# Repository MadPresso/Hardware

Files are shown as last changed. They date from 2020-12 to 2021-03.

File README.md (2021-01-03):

# MadPresso

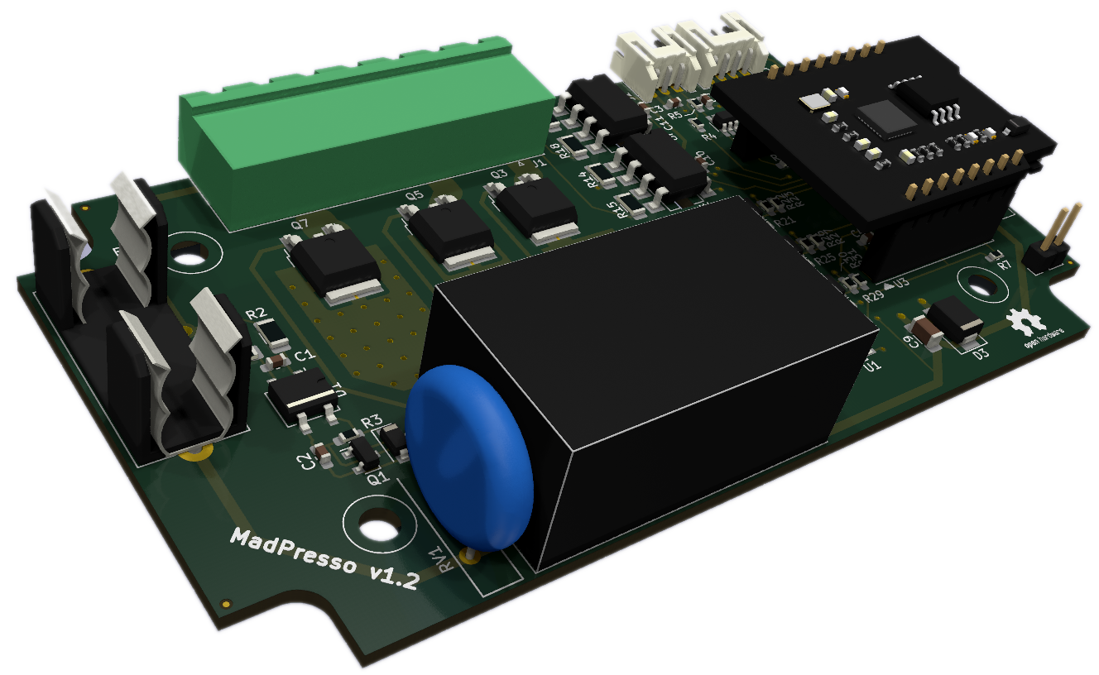
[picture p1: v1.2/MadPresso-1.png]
3D image of PCB


MadPresso is an open-hardware [PID controller](https://en.wikipedia.org/wiki/PID_controller) for espresso machines, based on an ESP8266 module. It was developed for a [Rancilio Silvia](https://www.ranciliogroup.com/rancilio/silvia/silvia/) machine but is likely usable with other brands as well.

This repository contains the [KiCad](https://kicad.org) hardware design files

Open Hardware logo
KiCad logo

# Features

* Compatible with 110 VAC and 230 VAC mains, both 50 Hz and 60 Hz
* ESP8266 module for controlling logic, Wifi and logging
* Fused 5V power supply
* Zero-crossing logic for phase-cutting time base
* 2 Triac outputs for LINE switching
* 1 Triac output for NEUTRAL switching
* 2 main voltage monitors on LINE
* 3-pin JST connector for LM35DT temperature sensor
* 4-pin JST connector for general purpose peripherals such as an OLED display

# Functionality

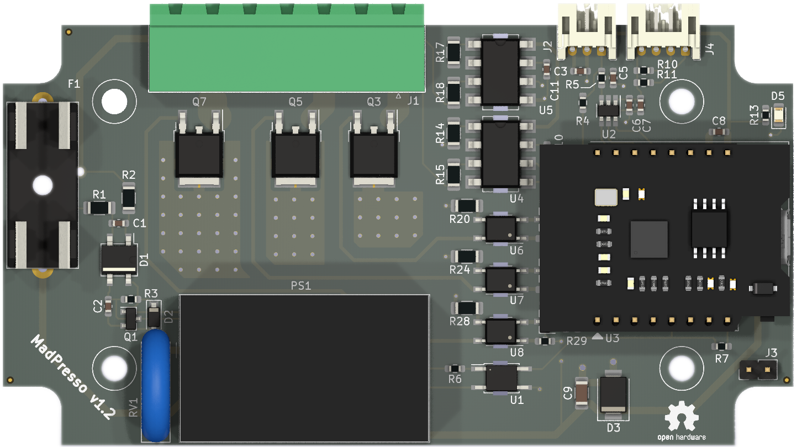
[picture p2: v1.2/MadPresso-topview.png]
PCB top view


The design features a zero-crossing detection circuitry that generates short spikes of low pulses around the point in time when the mains voltages crosses the zero-point. This signal is fed to the ESP8266 module which uses it to reset the triac ignition timer. Refer to the [firmware project](https://github.com/MadPresso/Firmware) for more details.

The boiler temperature is measured with an [LM35DT](https://www.ti.com/lit/ds/symlink/lm35.pdf) and sampled with a 10-bit ADC. The value is used as input to the PID logic implemented in the [firmware](https://github.com/MadPresso/Firmware).

Triac are controlled by the firmware as well, and isolated from the digital part through optocouplers.

Two line-monitor voltage sensors are used to detect the state of the "Shot" and "Steam" switches. Both are isolated from the digital logic through optocouplers as well.

# Pinout

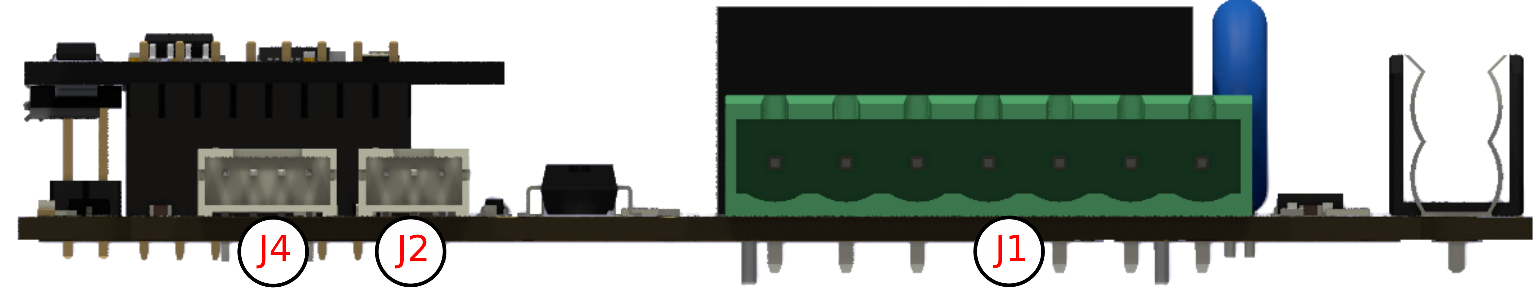
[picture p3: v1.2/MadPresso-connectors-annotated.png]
Connectors view annotated


The connectors located on the upper side of the PCB have the following functions. Note that pin 1 is on the left side of the connector when looked at as shown in the picture.

## J1

This connector carries all the 230 VAC mains functions. 
The mating part is an [RS Pro 8971222 Pluggable Rising Clamp Terminal](https://docs.rs-online.com/e4b6/0900766b8157d651.pdf).

1. Triac switch contact for NEUTRAL switching (LINE is permantely connected at the consumer). This pin is used to switch the **pump** on the Rancilio Silvia model.
2. NEUTRAL mains connection
3. Triac switch contact for LINE switchon (NEUTRAL is permanently connected at the consumer). This pin is used to switch the **valve** on the Rancilio Silvia model.
4. Shot switch LINE end
5. Steam switch LINE end
6. Triac switch contact for LINE switchon (NEUTRAL is permanently connected at the consumer). This pin is used to switch the **heater** on the Rancilio Silvia model.
7. LINE mains connection

## J2

This connector is intended to be used with an [LM35DT](https://www.ti.com/lit/ds/symlink/lm35.pdf) analog temperature sensor.
The mating part is a 3-pin, 2mm pitch [JST PH](http://www.jst-mfg.com/product/detail_e.php?series=199) plug.

1. Analog temperature input pin
2. GND
3. +5V

## J4

This connector is a general-purpose I²C extension that may be used to connect an OLED display, for instance.
The mating part is a 4-pin, 2mm pitch [JST PH](http://www.jst-mfg.com/product/detail_e.php?series=199) plug.

1. SDA
2. SCL
3. GND
4. +3.3V

# Housing

The PCB is made to fit into a [Hammond 1591XXBT](http://hammondmfg.com/dwg2XX.htm) plastic case. Cut-outs need to be milled into the case for the connectors.

# Schematics

The schematics are provided as [PDF](https://github.com/MadPresso/Hardware/blob/main/v1.2/MadPresso.pdf) and as KiCad design file.

# License

The design is released under the [CC-BY-SA-NC license](https://creativecommons.org/licenses/by-nc-sa/3.0/). Commercial use is hence prohibited.

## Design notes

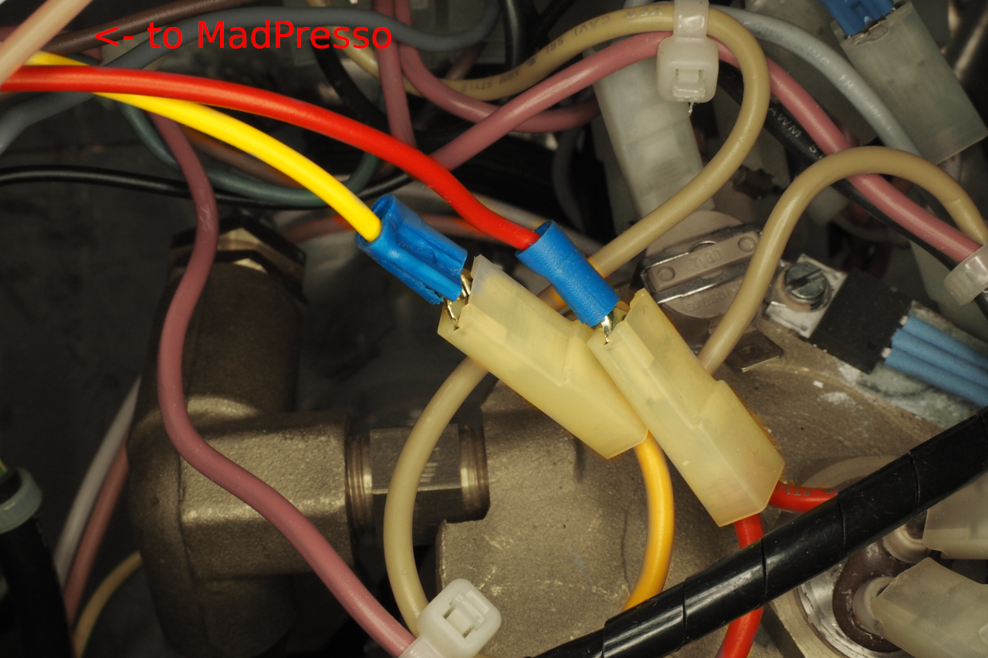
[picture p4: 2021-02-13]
doc/RancilioSilvia/connection-red-yellow.png

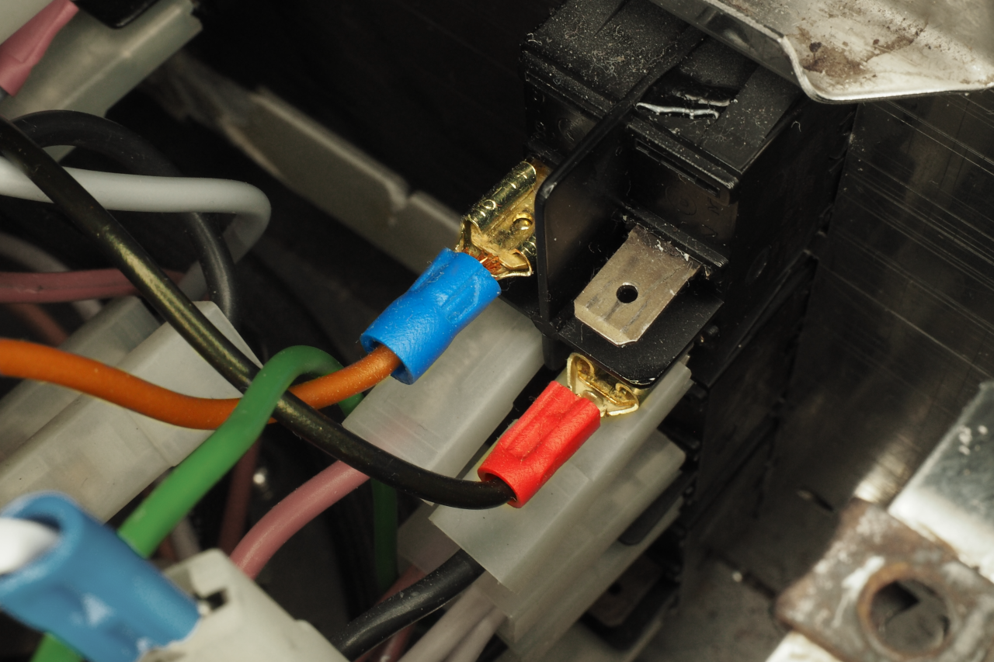
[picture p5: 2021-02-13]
doc/RancilioSilvia/connection-black-brown.png

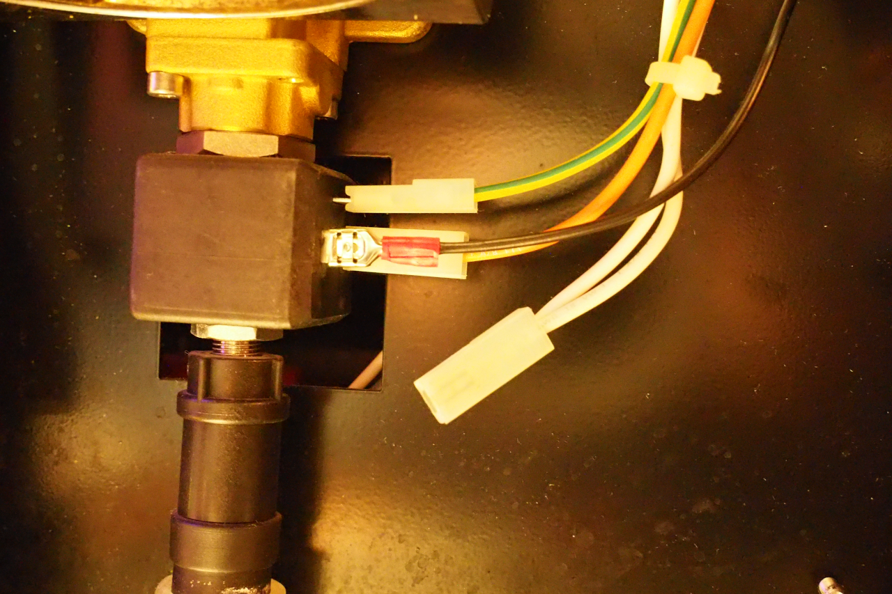
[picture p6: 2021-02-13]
doc/RancilioSilvia/connection-black-valve.png

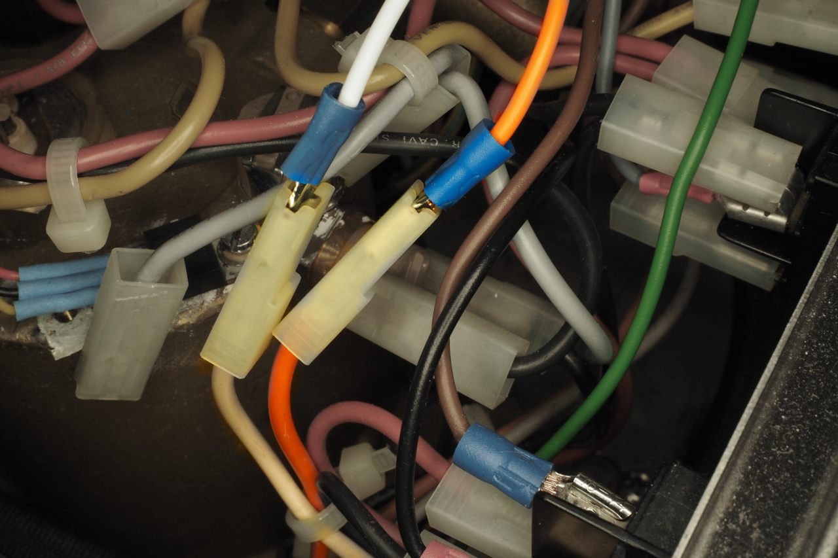
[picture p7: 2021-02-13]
doc/RancilioSilvia/connection-orange-white.png

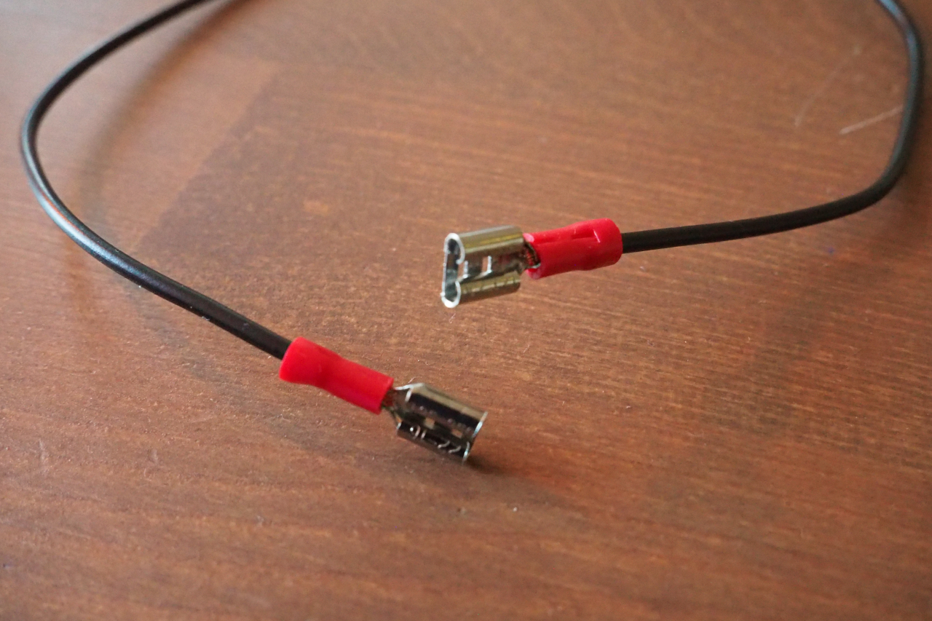
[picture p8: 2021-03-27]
doc/RancilioSilvia/cable-black.png

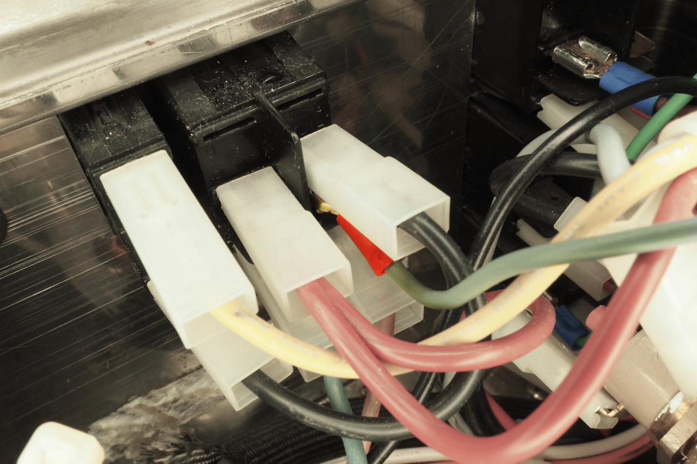
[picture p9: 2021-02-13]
doc/RancilioSilvia/connection-gray.png

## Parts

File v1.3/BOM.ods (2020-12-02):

Reference | Quantity | Value | Distributor | Distributor Item Number | Unit price (@5) | Total price (@5) | Footprint | Datasheet
C1 | 1 | 1nF | RS | 6983245 | 0.05 € | 0.05 € | Capacitor_SMD:C_0603_1608Metric_Pad1.08x0.95mm_HandSolder | ~
C2 | 1 | 10uF | RS | 536-9859 | 0.25 € | 0.25 € | Capacitor_SMD:CP_Elec_4x5.8 | ~
C3 C6 | 2 | 100nF | RS | 264-4630 | 0.07 € | 0.14 € | Capacitor_SMD:C_0603_1608Metric_Pad1.08x0.95mm_HandSolder | ~
C4 C10 C11 | 3 | DNP |  |  |  | 0.00 € | Capacitor_SMD:C_0603_1608Metric_Pad1.08x0.95mm_HandSolder | ~
C5 | 1 | 470pF | RS | 7880459 | 0.20 € | 0.20 € | Capacitor_SMD:C_0603_1608Metric_Pad1.08x0.95mm_HandSolder | ~
C7 | 1 | 4.7uF | RS | 8151351 | 0.35 € | 0.35 € | Capacitor_SMD:C_0603_1608Metric_Pad1.08x0.95mm_HandSolder | ~
C8 | 1 | 1uF | RS | 723-4972 | 0.17 € | 0.17 € | Capacitor_SMD:C_0603_1608Metric_Pad1.08x0.95mm_HandSolder | ~
C9 | 1 | 150uF | RS | 795-5196 | 1.52 € | 1.52 € | Capacitor_SMD:CP_Elec_8x10 | ~
D1 | 1 | MB6S | RS | 7613379 | 0.33 € | 0.33 € | Package_TO_SOT_SMD:TO-269AA | http://www.vishay.com/docs/88573/dfs.pdf
D2 | 1 | 1N4148W | RS | 700-3671 | 0.07 € | 0.07 € | Diode_SMD:D_SOD-123 | https://www.vishay.com/docs/85748/1n4148w.pdf
D3 | 1 | SMBJ7.0A | RS | 1714355 | 0.25 € | 0.25 € | Diode_SMD:D_SMB | https://www.st.com/resource/en/datasheet/sm6t.pdf
D4 D5 | 2 | LED | RS | 466-3778 | 0.34 € | 0.68 € | LED_SMD:LED_0805_2012Metric_Pad1.15x1.40mm_HandSolder | ~
F1 | 1 | 0.2A/250V | RS | 769-0149 | 0.70 € | 0.70 € | Fuse:Fuseholder_Cylinder-5x20mm_Schurter_0031_8201_Horizontal_Open | ~
J1 | 1 | Conn_01x07 | RS | 897-1281 |  | 0.00 € | Connector_Phoenix_MSTB:PhoenixContact_MSTBA_2,5_7-G-5,08_1x07_P5.08mm_Horizontal | ~
J2 | 1 | Conn_01x03 | RS | 820-1504 |  | 0.00 € | Connector_JST:JST_PH_S3B-PH-K_1x03_P2.00mm_Horizontal | ~
J3 | 1 | Conn_01x02 |  |  |  | 0.00 € | Connector_PinHeader_2.54mm:PinHeader_1x02_P2.54mm_Vertical | ~
J4 | 1 | Conn_01x04 | RS | 8201507 | 0.49 € | 0.49 € | Connector_JST:JST_PH_S4B-PH-K_1x04_P2.00mm_Horizontal | ~
PS1 | 1 | HLK-PM01 | makershop.de |  | 4.00 € | 4.00 € | Converter_ACDC:Converter_ACDC_HiLink_HLK-PMxx | http://www.hlktech.net/product_detail.php?ProId=54
Q1 | 1 | BC847 | RS | 690-0091 | 0.09 € | 0.09 € | Package_TO_SOT_SMD:SOT-23 | http://www.infineon.com/dgdl/Infineon-BC847SERIES_BC848SERIES_BC849SERIES_BC850SERIES-DS-v01_01-en.pdf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
Q2 | 1 | BSS84 | RS | 6710328 | 0.24 € | 0.24 € | Package_TO_SOT_SMD:SOT-23 | http://assets.nexperia.com/documents/data-sheet/BSS84.pdf
Q3 Q5 Q7 | 3 | T835-600B | RS | 8805487 | 1.00 € | 3.00 € | Package_TO_SOT_SMD:TO-252-2 | https://assets.nexperia.com/documents/data-sheet/BT138_SER_D_E.pdf
Q4 Q6 Q8 | 3 | 2N7002 | RS | 436-7379 | 0.12 € | 0.36 € | Package_TO_SOT_SMD:SOT-23 | https://www.onsemi.com/pub/Collateral/NDS7002A-D.PDF
R1 R2 | 2 | 220k | RS | 223-2574 | 0.01 € | 0.02 € | Resistor_SMD:R_1206_3216Metric_Pad1.30x1.75mm_HandSolder | ~
R10 R11 | 2 | 3k3 |  |  |  | 0.00 € | Resistor_SMD:R_0603_1608Metric_Pad0.98x0.95mm_HandSolder | ~
R12 | 1 | 220 |  |  |  | 0.00 € | Resistor_SMD:R_0603_1608Metric_Pad0.98x0.95mm_HandSolder | ~
R13 R16 R19 | 3 | 330 |  |  |  | 0.00 € | Resistor_SMD:R_0603_1608Metric_Pad0.98x0.95mm_HandSolder | ~
R14 R17 | 2 | 22k/0.5W | RS | 8121843 | 0.02 € | 0.04 € | Resistor_SMD:R_1206_3216Metric_Pad1.30x1.75mm_HandSolder | ~
R15 R18 | 2 | 33k/0.5W | RS | 6792055 | 0.10 € | 0.20 € | Resistor_SMD:R_1206_3216Metric_Pad1.30x1.75mm_HandSolder | ~
R20 R24 R28 | 3 | 360R/0.5W | RS | 7219787 | 0.25 € | 0.75 € | Resistor_SMD:R_1206_3216Metric_Pad1.30x1.75mm_HandSolder | https://docs.rs-online.com/ef78/0900766b812cb812.pdf | Panasonic ERJP08F3600V
R21 R25 R29 | 3 | 360R |  |  |  | 0.00 € | Resistor_SMD:R_0603_1608Metric_Pad0.98x0.95mm_HandSolder | ~
R22 R26 R30 | 3 | 10k |  |  |  | 0.00 € | Resistor_SMD:R_0603_1608Metric_Pad0.98x0.95mm_HandSolder | ~
R3 | 1 | 22k |  |  |  | 0.00 € | Resistor_SMD:R_0603_1608Metric_Pad0.98x0.95mm_HandSolder | ~
R4 R8 | 2 | DNP |  |  |  | 0.00 € | Resistor_SMD:R_0603_1608Metric_Pad0.98x0.95mm_HandSolder | ~
R5 | 1 | 22R |  |  |  | 0.00 € | Resistor_SMD:R_0603_1608Metric_Pad0.98x0.95mm_HandSolder | ~
R6 R9 R23 R27 R31 | 5 | 1k |  |  |  | 0.00 € | Resistor_SMD:R_0603_1608Metric_Pad0.98x0.95mm_HandSolder | ~
R7 | 1 | 4k7 |  |  |  | 0.00 € | Resistor_SMD:R_0603_1608Metric_Pad0.98x0.95mm_HandSolder | ~
RV1 | 1 | S14K350 | RS | 7691524 | 0.37 € | 0.37 € | Varistor:RV_Disc_D15.5mm_W3.9mm_P7.5mm | ~
U1 | 1 | LTV-356T | RS | 691-2079 | 0.19 € | 0.19 € | Package_SO:SO-4_4.4x3.6mm_P2.54mm | http://optoelectronics.liteon.com/upload/download/DS70-2001-010/S_110_LTV-356T%2020140520.pdf
U2 | 1 | ADC101C021CIMK | RS | 6394137 | 2.32 € | 2.32 € | Package_TO_SOT_SMD:SOT-23-6_Handsoldering | https://www.ti.com/lit/ds/symlink/adc101c021.pdf
U3 | 1 | WeMos_D1_mini | AZ delivery |  | 4.00 € | 4.00 € | Module:WEMOS_D1_mini_light | https://wiki.wemos.cc/products:d1:d1_mini#documentation
U4 U5 | 2 | MID400 | RS | 862-9381 | 1.39 € | 2.77 € | Package_DIP:SMDIP-8_W7.62mm | https://www.onsemi.com/pub/Collateral/MID400-D.pdf
U6 U7 U8 | 3 | TLP160G | RS | 760-3182 | 0.69 € | 2.07 € | Package_SO:MFSOP6-4_4.4x3.6mm_P1.27mm | https://toshiba.semicon-storage.com/info/docget.jsp?did=16916&prodName=TLP160G
 |  |  |  |  |  | 0.00 €
 |  |  |  |  |  | 0.00 €
 |  |  |  |  |  | 0.00 €
Fuse 0.2A/250V | 1 |  | RS | 7777485 | 0.07 € | 0.07 €
Hammond case | 1 | 1591XXBT | Voelkner |  | 6.70 € | 6.70 €
LM35DT | 1 | LM35DT | RS | 535-9458 | 2.66 € | 2.66 €
7-pin connector header | 1 |  | RS | 897-1222 | 1.78 € | 1.78 €
PCB | 1 |  | PCBway |  | 9.00 € | 9.00 €
 |  |  |  |  | Total net | 42.82 €
 |  |  |  |  | Total gross | 49.67 €

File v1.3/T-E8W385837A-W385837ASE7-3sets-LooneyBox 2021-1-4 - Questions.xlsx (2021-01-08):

3sets | PCBWay Comments | Your Reply | Reference | Quantity | Value | Manufacturer | Partnum | Footprint | DESCRIPTION | SMD/THT | Datasheet
$0.105 |  |  | C1 C2 C3 C5 C24 | 5 | 0.1uF |  |  | Capacitor_SMD:C_0603_1608Metric_Pad1.08x0.95mm_HandSolder | Ceramic capacitor X7R | SMD
$0.210 |  |  | C12 | 1 | 0.47uF |  |  | Capacitor_SMD:C_0603_1608Metric_Pad1.08x0.95mm_HandSolder | Ceramic capacitor X7R | SMD
$0.105 |  |  | C16 | 1 | 100nF |  |  | Capacitor_SMD:C_0603_1608Metric_Pad1.08x0.95mm_HandSolder | Ceramic capacitor X7R | SMD
$0.315 |  |  | C4 C14 C18 C23 | 4 | 10uF |  |  | Capacitor_SMD:C_0603_1608Metric_Pad1.08x0.95mm_HandSolder | Ceramic capacitor X7R | SMD
$0.105 |  |  | C6 C9 C10 C11 C13 C15 C17 C19 C20 C21 C22 | 11 | 1uF |  |  | Capacitor_SMD:C_0603_1608Metric_Pad1.08x0.95mm_HandSolder | Ceramic capacitor X7R | SMD
$0.210 |  |  | C7 | 1 | 2.2uF |  |  | Capacitor_SMD:C_0603_1608Metric_Pad1.08x0.95mm_HandSolder | Ceramic capacitor X7R | SMD
$0.315 |  |  | C8 C25 | 2 | 22uF |  |  | Capacitor_SMD:C_0805_2012Metric_Pad1.18x1.45mm_HandSolder | Ceramic capacitor X7R | SMD
$1.575 | 5-7work days | feel free to replace with other 0603 LED (blue) | D1 | 1 | LED blue | Kingbright | APHD1608LVBC/D | LED_SMD:LED_0603_1608Metric_Pad1.05x0.95mm_HandSolder | LED blue | SMD
$1.155 | 5-7work days | feel free to replace with other 0603 LED (green) | D3 | 1 | LED green | Kingbright | APHD1608LCGCK | LED_SMD:LED_0603_1608Metric_Pad1.05x0.95mm_HandSolder | LED green | SMD
$1.260 | 5-7work days | feel free to replace with other 0603 LED (red) | D5 | 1 | LED red | Kingbright | APHD1608LSURCK | LED_SMD:LED_0603_1608Metric_Pad1.05x0.95mm_HandSolder | LED red | SMD
$0.315 | provide with B5817WS-TP 1000pcs in stock |  | D2 | 1 | B5819 | MCC | B5819 | Diode_SMD:D_SOD-323 |  | SMD | https://www.mouser.de/datasheet/2/258/B5817WS-B5819WS(SOD-323)-V2-1626103.pdf
$0.315 |  |  | D4 | 1 | SMBJ6.0A | Vishay | SMBJ6.0A | Diode_SMD:D_SMB |  | SMD | https://www.st.com/resource/en/datasheet/sm6t.pdf
$2.520 | 5-7work days |  | J1 | 1 | Micro_SD_Card_Det | Molex | 104031-0811 | Connector_Card:microSD_HC_Molex_104031-0811 |  | SMD | https://www.hirose.com/product/en/download_file/key_name/DM3/category/Catalog/doc_file_id/49662/?item_id=195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
$0.525 | provide with B3B-PH-K-S(LF)(SN) please confirm | ok | J10 J14 J15 | 3 | Conn_01x03 | JST | B3B-PH-K | Connector_JST:JST_PH_B3B-PH-K_1x03_P2.00mm_Vertical |  | THT
$0.315 | provide with B6B-PH-K(LF)(SN) 500pcs in stock |  | J11 | 1 | Conn_01x06 | JST | B6B-PH-K | Connector_JST:JST_PH_B6B-PH-K_1x06_P2.00mm_Vertical |  | THT
$0.210 | provide with pin header 1*8pin 2.54mm |  | J13 | 1 | Conn_01x08 |  |  | Connector_PinSocket_2.54mm:PinSocket_1x08_P2.54mm_Vertical |  | THT
$1.890 | provide with USB4085-GF-A 5-7work days |  | J2 | 1 | USB_C_Receptacle_USB2.0 | GCT | USB4085 | Connector_USB:USB_C_Receptacle_GCT_USB4085 | USB-C receptacle | THT | https://www.usb.org/sites/default/files/documents/usb_type-c.zip
$1.680 | provide with SJ1-3514-SMT-TR 5-7work days |  | J3 | 1 | SJ1-3514-SMT | CUI Devices | SJ1-3514-SMT | LonleyBox:CUI_SJ1-3514-SMT | 3.5mm headphone receptacle | SMD
$0.105 | provide with B2B-PH-K-S(LF)(SN) 1000pcs in stock, please confirm | ok | J4 J6 J7 J12 J16 J17 | 6 | Conn_01x02 | JST | B2B-PH-K | Connector_JST:JST_PH_B2B-PH-K_1x02_P2.00mm_Vertical |  | THT
$0.210 | provide with B4B-PH-K(LF)(SN)1000pcs in stock |  | J5 J9 | 2 | Conn_01x04 | JST | B4B-PH-K | Connector_JST:JST_PH_B4B-PH-K_1x04_P2.00mm_Vertical |  | THT
$0.210 | provide with pin header 1*4pin 2.54mm |  | J8 | 1 | Conn_01x04 |  |  | Connector_PinSocket_2.54mm:PinSocket_1x04_P2.54mm_Vertical |  | THT
$0.210 | provide with pin header 1*2pin 2.54mm |  | JP1 | 1 | Jumper_2_Open |  |  | Connector_PinHeader_2.54mm:PinHeader_1x02_P2.54mm_Vertical |  | THT
$1.575 | provide with XFL4020-222MEC |  | L1 | 1 | 2.2 uH | Coilcraft | XFL4020222ME | Inductor_SMD:L_Coilcraft_XxL4020 |  | SMD | https://www.coilcraft.com/getmedia/50632d43-da1b-4cdb-8ab4-3029cab51df3/xfl4020.pdf
$0.420 | 1000pcs in stock |  | Q1 | 1 | UMH3N | Rohm | UMH3N | Package_TO_SOT_SMD:SOT-363_SC-70-6 |  | SMD | http://rohmfs.rohm.com/en/products/databook/datasheet/discrete/transistor/digital/emh3t2r-e.pdf
 | no stock, do you have any other alternative? | OnSemi MUN5216T1G | Q2 | 1 | DTC143TUA | Rohm | DTS143TUA | Package_TO_SOT_SMD:SOT-323_SC-70 |  | SMD | http://rohmfs.rohm.com/en/products/databook/datasheet/discrete/transistor/digital/dtc143t.pdf
$0.420 | provide with SI2371EDS-T1-GE3 |  | Q3 | 1 | Si2371EDS | Vishay | Si2371EDS | Package_TO_SOT_SMD:SOT-23 |  | SMD | http://www.vishay.com/docs/63924/si2371eds.pdf
$0.105 |  |  | R1 R20 R21 R25 R26 | 5 | 100k |  |  | Resistor_SMD:R_0603_1608Metric_Pad0.98x0.95mm_HandSolder | Resistor thin-film, 0.125W, 1% | SMD
$0.105 |  |  | R14 | 1 | 100R |  |  | Resistor_SMD:R_0603_1608Metric_Pad0.98x0.95mm_HandSolder | Resistor thin-film, 0.125W, 1% | SMD
 | not mount |  | R15 R28 R29 R30 R31 | 5 | DNP |  |  | Resistor_SMD:R_0603_1608Metric_Pad0.98x0.95mm_HandSolder | Resistor thin-film, 0.125W, 1% | SMD
$0.105 |  |  | R16 R22 | 2 | 0R |  |  | Resistor_SMD:R_0603_1608Metric_Pad0.98x0.95mm_HandSolder | Resistor thin-film, 0.125W, 1% | SMD
$0.105 |  |  | R18 R19 | 2 | 5.1k |  |  | Resistor_SMD:R_0603_1608Metric_Pad0.98x0.95mm_HandSolder | Resistor thin-film, 0.125W, 1% | SMD
$0.105 |  |  | R2 R17 R23 R24 | 4 | 2k |  |  | Resistor_SMD:R_0603_1608Metric_Pad0.98x0.95mm_HandSolder | Resistor thin-film, 0.125W, 1% | SMD
$0.210 |  |  | R27 | 1 | 0.1R |  |  | Resistor_SMD:R_1206_3216Metric_Pad1.30x1.75mm_HandSolder | Resistor thin-film, 0.5W, 1% | SMD
$0.105 |  |  | R3 R4 R5 R8 R9 R10 R11 R12 R13 | 9 | 10k |  |  | Resistor_SMD:R_0603_1608Metric_Pad0.98x0.95mm_HandSolder | Resistor thin-film, 0.125W, 1% | SMD
$0.105 |  |  | R6 R7 | 2 | 3k3 |  |  | Resistor_SMD:R_0603_1608Metric_Pad0.98x0.95mm_HandSolder | Resistor thin-film, 0.125W, 1% | SMD
 | could you please provide with detailed part number or digikey/mouser link for our check? | https://www.digikey.com/en/products/detail/panasonic-electronic-components/EVQ-P2B02B/593466 | SW1 | 1 | SW_Push | Panasonic | EVQP2 | Button_Switch_SMD:SW_SPST_EVQP2 | Push button | SMD
$0.840 |  |  | U1 U3 U6 U10 U11 U12 | 6 | SRV05-4 | OnSemi | SRV05-4MR6T1G | Package_TO_SOT_SMD:SOT-23-6 |  | SMD | http://www.onsemi.com/pub/Collateral/SRV05-4-D.PDF
$5.250 | ESP32-WROOM-32 4mb falsh |  | U2 | 1 | ESP32-WROOM-32 | Espressif | ESP32-WROOM-32 | RF_Module:ESP32-WROOM-32 | ESP32 module | SMD | https://www.espressif.com/sites/default/files/documentation/esp32-wroom-32_datasheet_en.pdf
$1.575 | provide with TPS63001DRCR |  | U4 | 1 | TPS63001 | TI | TPS63001 | Package_SON:Texas_DRC0010J_ThermalVias |  | SMD | http://www.ti.com/lit/ds/symlink/tps63000.pdf
$6.300 | provide with MAX9850ETI+T 5-7work days |  | U5 | 1 | MAX9850ETI+ | Maxim | MAX9850ETI+ | Package_DFN_QFN:TQFN-28-1EP_5x5mm_P0.5mm_EP3.25x3.25mm |  | SMD | https://datasheets.maximintegrated.com/en/ds/MAX9850.pdf
$0.840 |  |  | U7 | 1 | CH340C | Jiangsu | CH340C | Package_SO:SOIC-16_3.9x9.9mm_P1.27mm |  | SMD | https://datasheet.lcsc.com/szlcsc/Jiangsu-Qin-Heng-CH340C_C84681.pdf
$3.150 |  |  | U8 | 1 | LTC4054ES5-4.2 | Analog Devices | LTC4054ES5-4.2 | Package_TO_SOT_SMD:TSOT-23-5 |  | SMD | https://www.analog.com/media/en/technical-documentation/data-sheets/405442xf.pdf
$1.240 | provide with MAX98306ETD+T please confirm 3-4work days | ok | U9 | 1 | MAX98306EDT+ | Maxim | MAX98306EDT+ | Package_DFN_QFN:TDFN-14-1EP_3x3mm_P0.4mm_EP1.78x2.35mm_ThermalVias |  | SMD | https://datasheets.maximintegrated.com/en/ds/MAX98306.pdf
according to Partnum |  |  |  | 96

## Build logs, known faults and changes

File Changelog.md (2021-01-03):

# Changelog v1.1 → v1.2

* Thicker thermal connectors on LINE power plane, amended clearance a bit
* Fix Q2 polarity
* Add open hardware logo
* Add back KiCad logo
* Make pump triac switch NEUT instead of LINE
* Improve clearance
* Make all capacitors ceramic types

# Changelog v1 → v1.1

* Replace 4 1N4148 with MD6S bridge rectifier
* Changed footprint of MID400 to SMD
* Add another 22k input resistor for MID400, and change to 0.5W types
* Swap D8/D6 and D3/D5 on D1 module due to boot state restrictions
* Add LED to D4
* Add external I2C ADC as the internal ESP8266 ADC is not precise enough
* Update footprints for 0603 and 1206 resistors
* Improve AC clearance
* Move fuse before ZC detection logic
* Removed LEDs to free I2C lines
* Switch to SMD triacs
* Value changes in triac circuit

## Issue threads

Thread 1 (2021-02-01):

Triac in heater circuit may be overloaded

VaRe123, 2021-02-01:
Check carefully figure 3 of the datasheet of triac T835-600G:

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

When heating up you can't use the full 1150W of the heater as this would be equivalent to approx. 5 A RMS current! The D2PAK package in use is only capable of conducting 3 A RMS at max, even it is different stated in the header of the datasheet (8A RMS).

zonque, 2021-02-01:
Ah, thanks for spotting this! I've changed the Triac type to the one that was actually used during development (BT138-600).

VaRe123, 2021-02-01:
Do you use a heatsink than on this specific triac?

zonque, 2021-02-01:
Fischer ICK24B can be glued across on all 3 Triacs, yes. But as heat is dissipated well enough through the PCB, my measurements so far show only temperatures below 90°C on the package surface.

Closed 2021-02-01.

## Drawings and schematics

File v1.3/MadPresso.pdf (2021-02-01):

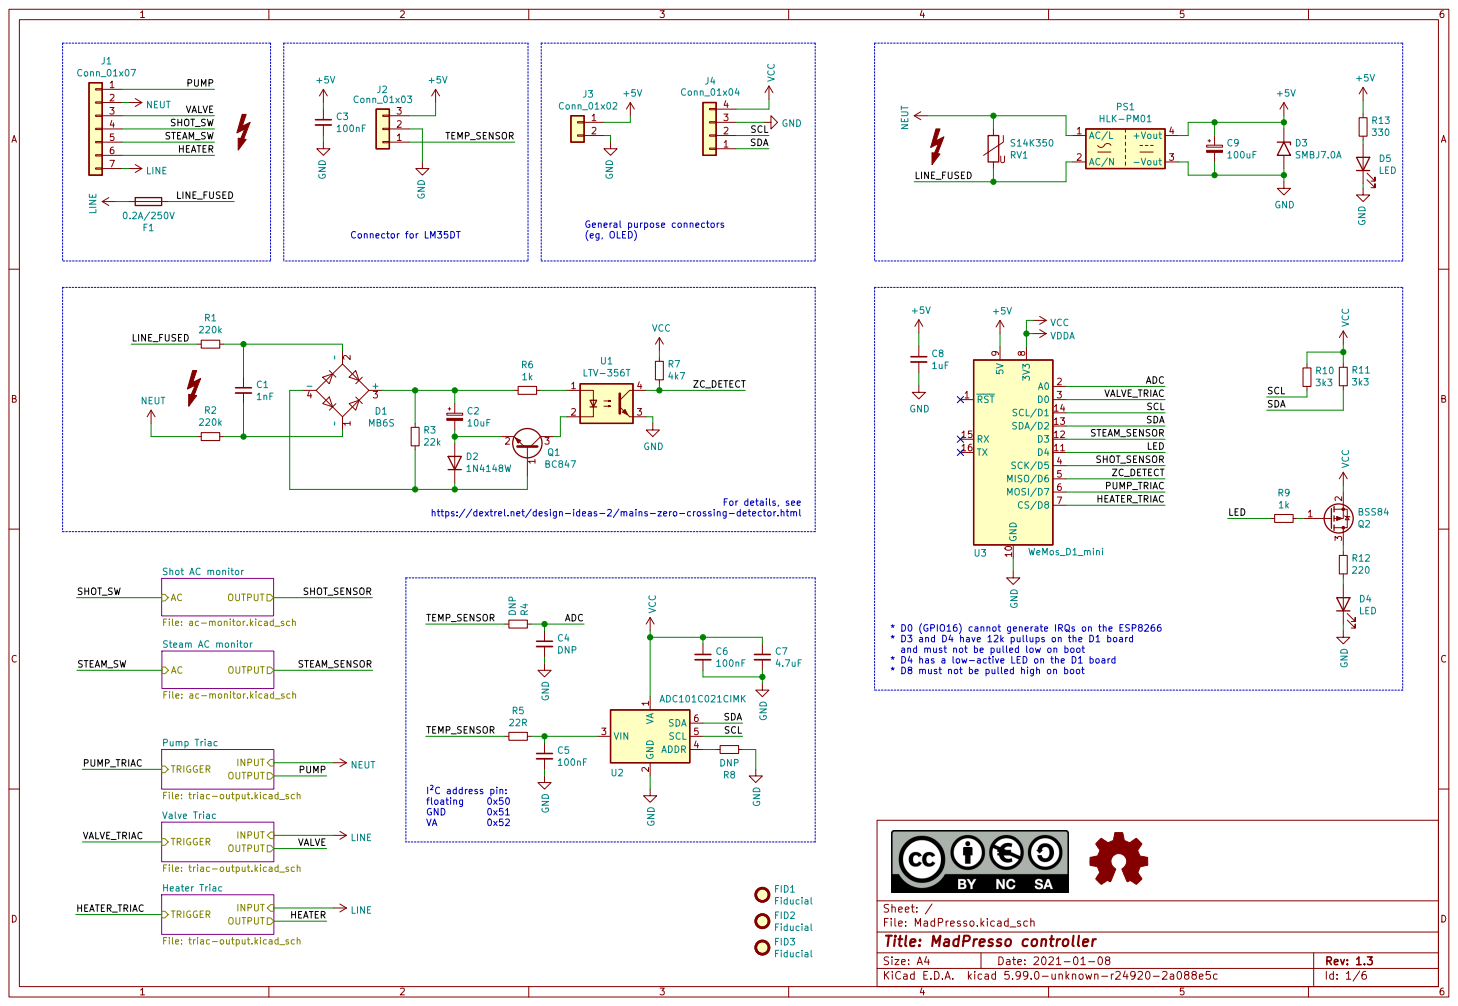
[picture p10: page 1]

FID2 Fiducial FID3 Fiducial VCC GND VA

https://dextrel.net/design-ideas-2/mains-zero-crossing-detector.html

* D0 (GPIO16) cannot generate IRQs on the ESP8266
* D3 and D4 have 12k pullups on the D1 board
and must not be pulled low on boot * D4 has a low-active LED on the D1 board

* D8 must not be pulled high on boot

2 VIN 3 ADDR 4 SCL 5 SDA 6 U2 ADC101C021CIMK GND

Id: 1/6 Title: MadPresso controller

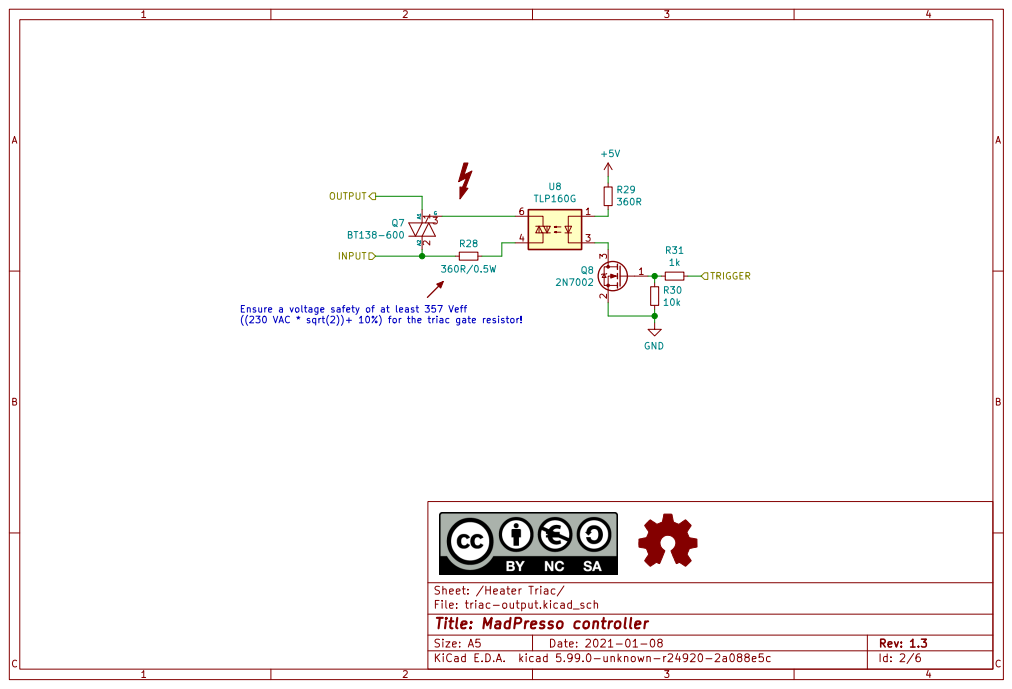
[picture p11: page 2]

INPUT Ensure a voltage safety of at least 357 Veff

((230 VAC * sqrt(2))+ 10%) for the triac gate resistor!

File: triac-output.kicad_sch Sheet: /Heater Triac/
Id: 2/6 Title: MadPresso controller

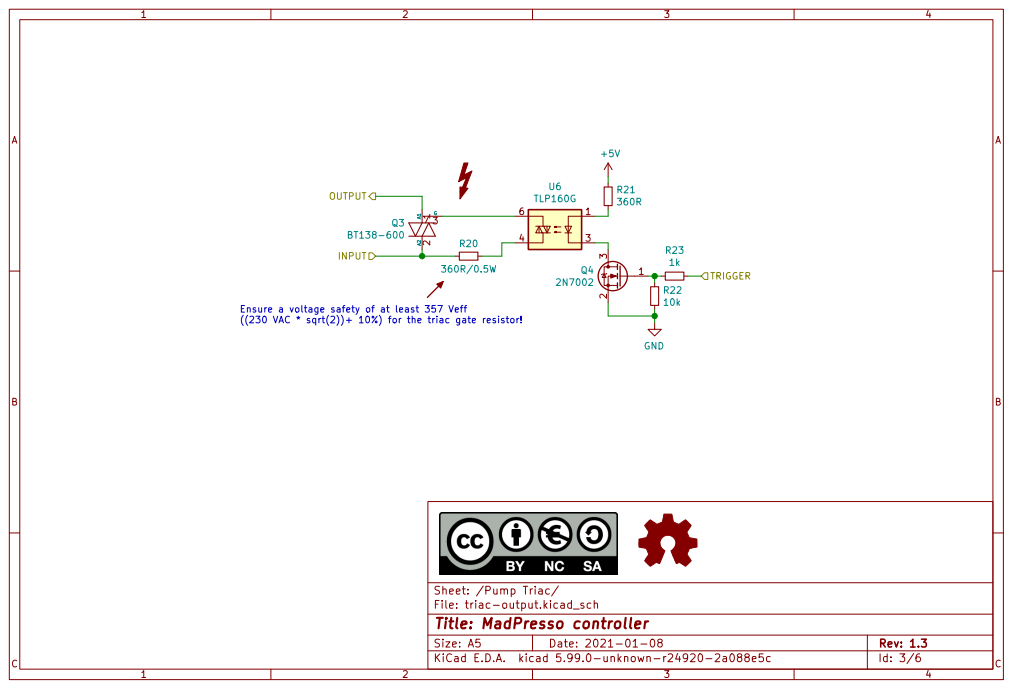
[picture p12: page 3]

INPUT Ensure a voltage safety of at least 357 Veff

((230 VAC * sqrt(2))+ 10%) for the triac gate resistor!

Sheet: /Pump Triac/
File: triac-output.kicad_sch
Id: 3/6 Title: MadPresso controller

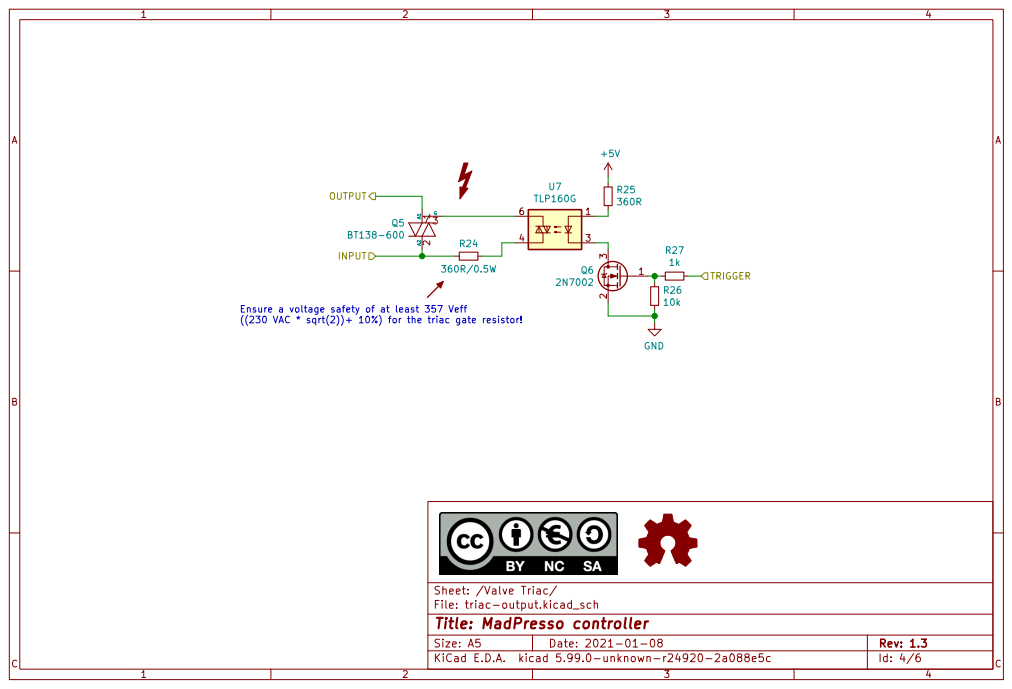
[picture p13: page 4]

INPUT Ensure a voltage safety of at least 357 Veff

((230 VAC * sqrt(2))+ 10%) for the triac gate resistor!

File: triac-output.kicad_sch Sheet: /Valve Triac/
Id: 4/6 Title: MadPresso controller

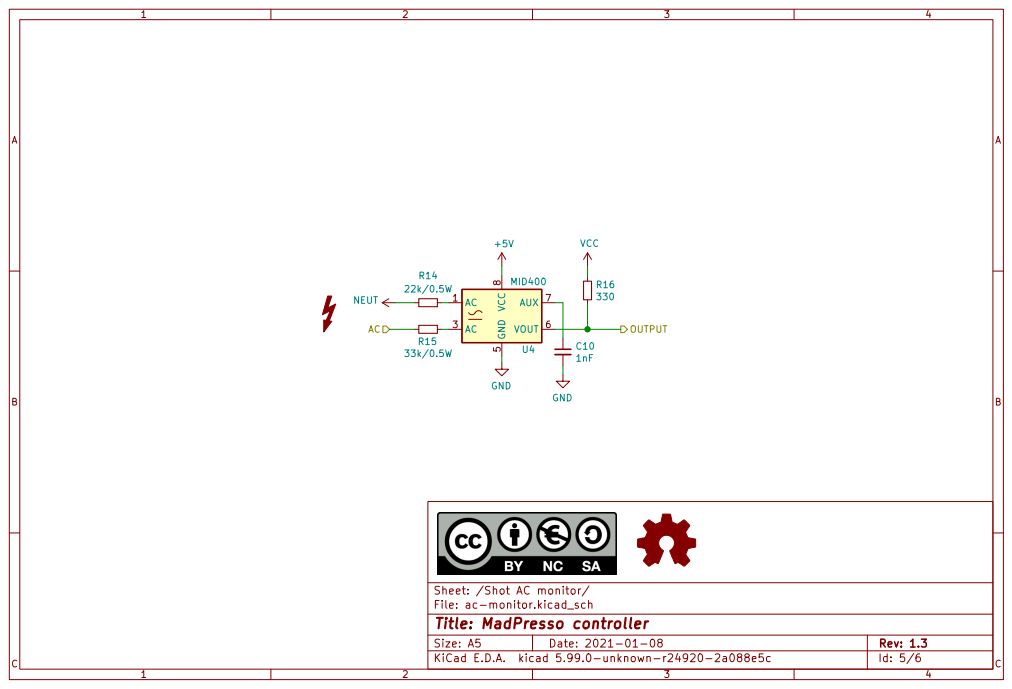
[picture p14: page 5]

File: ac-monitor.kicad_sch Sheet: /Shot AC monitor/ R15

Id: 5/6 Title: MadPresso controller

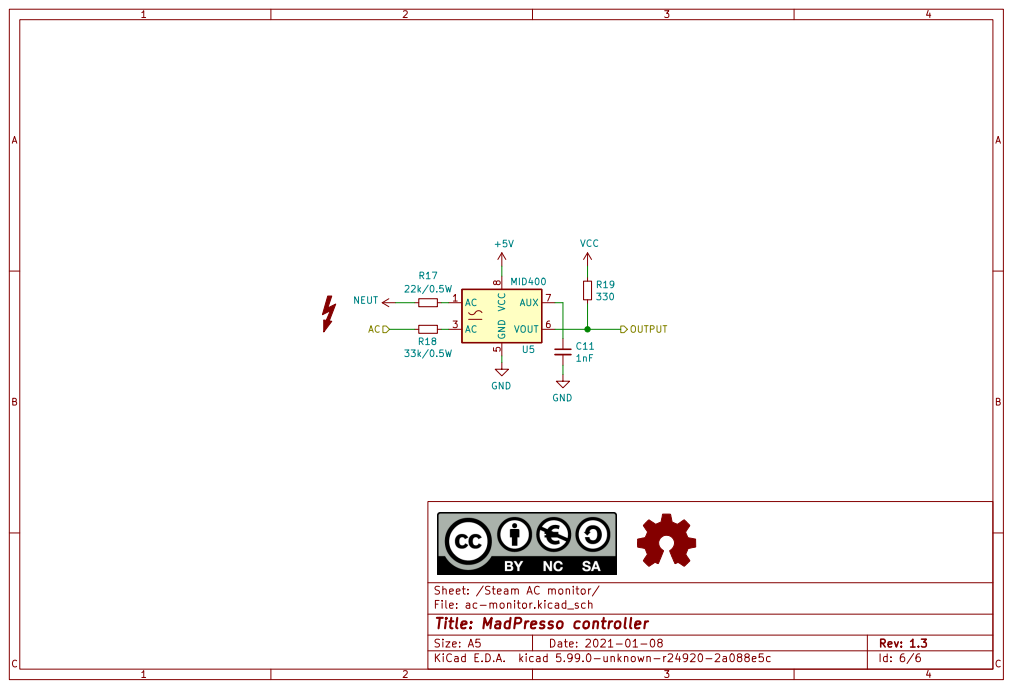
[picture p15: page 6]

File: ac-monitor.kicad_sch Sheet: /Steam AC monitor/ R18

Id: 6/6 Title: MadPresso controller

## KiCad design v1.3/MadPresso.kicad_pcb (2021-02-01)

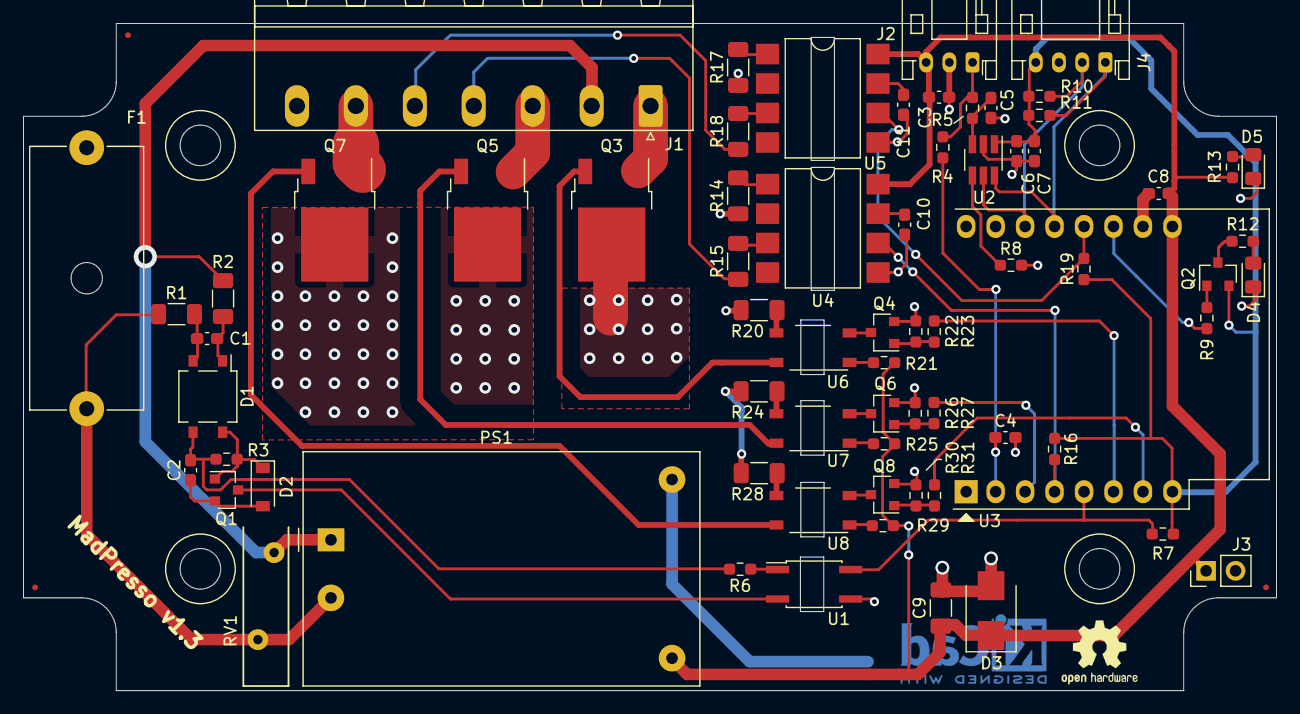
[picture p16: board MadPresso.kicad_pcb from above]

Board: 2 copper layers, 108.0 x 57.5 mm, 74 parts (0 on the bottom side), 56 nets.

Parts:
C1, C10, C11: 1nF; C_0603_1608Metric_Pad1.08x0.95mm_HandSolder
C2: 10uF; C_0603_1608Metric_Pad1.08x0.95mm_HandSolder
C3, C5, C6: 100nF; C_0603_1608Metric_Pad1.08x0.95mm_HandSolder
C4: DNP; C_0603_1608Metric_Pad1.08x0.95mm_HandSolder
C7: 4.7uF; C_0603_1608Metric_Pad1.08x0.95mm_HandSolder
C8: 1uF; C_0603_1608Metric_Pad1.08x0.95mm_HandSolder
C9: 100uF; C_1206_3216Metric_Pad1.33x1.80mm_HandSolder
Case: Hammond 1591XXB
D1: MB6S; TO-269AA
D2: 1N4148W; D_SOD-123
D3: SMBJ7.0A; D_SMB
D4, D5: LED; LED_0805_2012Metric_Pad1.15x1.40mm_HandSolder
F1: 0.2A/250V; Fuseholder_Cylinder-5x20mm_Schurter_0031_8201_Horizontal_Op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
FID1, FID2, FID3: Fiducial; Fiducial_0.5mm_Mask1mm
J1: Conn_01x07; PhoenixContact_MSTBA_2,5_7-G-5,08_1x07_P5.08mm_Horizontal
J2: Conn_01x03; JST_PH_S3B-PH-K_1x03_P2.00mm_Horizontal
J3: Conn_01x02; PinHeader_1x02_P2.54mm_Vertical
J4: Conn_01x04; JST_PH_S4B-PH-K_1x04_P2.00mm_Horizontal
PS1: HLK-PM01; Converter_ACDC_HiLink_HLK-PMxx
Q1: BC847; SOT-23
Q2: BSS84; SOT-23
Q3, Q5, Q7: T835-600B; TO-252-2
Q4, Q6, Q8: 2N7002; SOT-23
R1, R2: 220k; R_1206_3216Metric_Pad1.30x1.75mm_HandSolder
R3: 22k; R_0603_1608Metric_Pad0.98x0.95mm_HandSolder
R4, R8: DNP; R_0603_1608Metric_Pad0.98x0.95mm_HandSolder
R5: 22R; R_0603_1608Metric_Pad0.98x0.95mm_HandSolder
R6, R9, R23, R27, R31: 1k; R_0603_1608Metric_Pad0.98x0.95mm_HandSolder
R7: 4k7; R_0603_1608Metric_Pad0.98x0.95mm_HandSolder
R10, R11: 3k3; R_0603_1608Metric_Pad0.98x0.95mm_HandSolder
R12: 220; R_0603_1608Metric_Pad0.98x0.95mm_HandSolder
R13, R16, R19: 330; R_0603_1608Metric_Pad0.98x0.95mm_HandSolder
R14, R17: 22k/0.5W; R_1206_3216Metric_Pad1.30x1.75mm_HandSolder
R15, R18: 33k/0.5W; R_1206_3216Metric_Pad1.30x1.75mm_HandSolder
R20, R24, R28: 360R/0.5W; R_1206_3216Metric_Pad1.30x1.75mm_HandSolder
R21, R25, R29: 360R; R_0603_1608Metric_Pad0.98x0.95mm_HandSolder
R22, R26, R30: 10k; R_0603_1608Metric_Pad0.98x0.95mm_HandSolder
RV1: S14K350; RV_Disc_D15.5mm_W3.9mm_P7.5mm
U1: LTV-356T; SO-4_4.4x3.6mm_P2.54mm
U2: ADC101C021CIMK; SOT-23-6_Handsoldering
U3: WeMos_D1_mini; WEMOS_D1_mini_light
U4, U5: MID400; SMDIP-8_W9.53mm
U6, U7, U8: TLP160G; MFSOP6-4_4.4x3.6mm_P1.27mm

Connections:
+5V: C3.1, C8.1, C9.1, D3.1 (A1), J2.3, J3.1, PS1.4 (+Vout), R13.2, R21.2, R25.2, R29.2, U3.9 (5V), U4.8 (VCC), U5.8 (VCC)
/ADC: C4.1, R4.2, U3.2 (A0)
/HEATER: J1.6, Q7.1 (A1)
/HEATER_TRIAC: R31.1, U3.7 (CS/D8)
/LED: R9.1, U3.11 (D4)
/LINE_FUSED: F1.2, PS1.2 (AC/N), R1.1, RV1.2
/PUMP: J1.1, Q3.1 (A1)
/PUMP_TRIAC: R23.1, U3.6 (MOSI/D7)
/SCL: J4.2, R10.1, U2.5 (SCL), U3.14 (SCL/D1)
/SDA: J4.1, R11.1, U2.6 (SDA), U3.13 (SDA/D2)
/SHOT_SENSOR: R16.2, U3.4 (SCK/D5), U4.6 (VOUT)
/SHOT_SW: J1.4, R15.1
/STEAM_SENSOR: R19.2, U3.12 (D3), U5.6 (VOUT)
/STEAM_SW: J1.5, R18.1
/TEMP_SENSOR: J2.1, R4.1, R5.2
/VALVE: J1.3, Q5.1 (A1)
/VALVE_TRIAC: R27.1, U3.3 (D0)
/ZC_DETECT: R7.1, U1.4, U3.5 (MISO/D6)
GND: C3.2, C4.2, C5.2, C6.2, C7.2, C8.2, C9.2, C10.2, C11.2, D3.2 (A2), D4.1 (K), D5.1 (K), J2.2, J3.2, J4.3, PS1.3 (-Vout), Q4.2 (S), Q6.2 (S), Q8.2 (S), R8.2, R22.2, R26.2, R30.2, U1.3, U2.2 (GND), U3.10 (GND), U4.5 (GND), U5.5 (GND)
LINE: F1.1, J1.7, Q5.2 (A2), Q7.2 (A2), R24.2, R28.2
NEUT: J1.2, PS1.1 (AC/L), Q3.2 (A2), R2.1, R14.1, R17.1, R20.2, RV1.1
unnamed: C1.1, D1.2 (~~), R1.2
unnamed: C1.2, D1.1 (~~), R2.2
unnamed: C2.1, D1.3 (+), R3.2, R6.2
unnamed: C2.2, D2.2 (A), Q1.2 (E)
unnamed: C5.1, R5.1, U2.3 (VIN)
unnamed: C10.1, U4.7 (AUX)
unnamed: C11.1, U5.7 (AUX)
unnamed: D1.4 (-), D2.1 (K), Q1.1 (B), R3.1
unnamed: D4.2 (A), R12.1
unnamed: D5.2 (A), R13.1
unnamed: Q1.3 (C), U1.2
unnamed: Q2.1 (G), R9.2
unnamed: Q2.3 (D), R12.2
unnamed: Q3.3 (G), U6.6
unnamed: Q4.1 (G), R22.1, R23.2
unnamed: Q4.3 (D), U6.3
unnamed: Q5.3 (G), U7.6
unnamed: Q6.1 (G), R26.1, R27.2
unnamed: Q6.3 (D), U7.3
unnamed: Q7.3 (G), U8.6
unnamed: Q8.1 (G), R30.1, R31.2
unnamed: Q8.3 (D), U8.3
unnamed: R6.1, U1.1
unnamed: R8.1, U2.4 (ADDR)
unnamed: R14.2, U4.1 (AC)
unnamed: R15.2, U4.3 (AC)
unnamed: R17.2, U5.1 (AC)
unnamed: R18.2, U5.3 (AC)
unnamed: R20.1, U6.4
unnamed: R21.1, U6.1
unnamed: R24.1, U7.4
unnamed: R25.1, U7.1
unnamed: R28.1, U8.4
unnamed: R29.1, U8.1
VCC: C6.1, C7.1, J4.4, Q2.2 (S), R7.2, R10.2, R11.2, R16.1, R19.1, U2.1 (VA), U3.8 (3V3)

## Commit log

2020-10-30 silkscreen work
    [MadPresso.kicad_pcb]
2020-10-31 Add another blocker C
    [MadPresso.kicad_pcb, MadPresso.kicad_sch, ac-monitor.kicad_sch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]
2020-11-01 some resistor footpring changes
    [MadPresso.kicad_pcb, MadPresso.kicad_sch]
2020-11-01 more work
    [MadPresso.kicad_pcb, MadPresso.kicad_sch, ac-monitor.kicad_sch]
2020-11-01 mirror power traces on bottom layer
    [MadPresso.kicad_pcb]
2020-11-01 Update to new KiCad symbols, replace and turn D1 module
    [MadPresso.kicad_pcb, MadPresso.kicad_sch, ac-monitor.kicad_sch]
2020-11-01 update mid400 symbol
    [MadPresso.kicad_sch, ac-monitor.kicad_sch]
2020-11-02 Add some Rancilio Silvia wiring docs
2020-11-03 add vaux cap to mid400
    [MadPresso.kicad_pcb, MadPresso.kicad_sch, ac-monitor.kicad_sch]
2020-11-04 Move PCB outline and screw holes to footprint
    [MadPresso.kicad_pcb]
2020-11-05 final touches for v1
    [MadPresso.kicad_pcb, MadPresso.kicad_sch, ac-monitor.kicad_sch]
2020-11-05 Add BOM for v1
2020-11-12 Value change for v1
    [MadPresso.kicad_sch]
2020-11-15 rename v1 -> v1.0
    [MadPresso-B_Cu.gbr, MadPresso-B_Mask.gbr, MadPresso-B_Paste.gbr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]
2020-11-15 add 1.2
    [MadPresso-B_Cu.gbr, MadPresso-B_Mask.gbr, MadPresso-B_Paste.gbr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]
2020-11-15 cleanups all over
    [MadPresso.kicad_pcb, MadPresso.kicad_sch, ac-monitor.kicad_sch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]
2020-11-17 start rework to smd triac
    [BOM.ods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]
2020-11-17 more work on smd triac routing
    [MadPresso.kicad_pcb, MadPresso.kicad_sch, ac-monitor.kicad_sch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]
2020-11-17 more routing
    [MadPresso.kicad_pcb, MadPresso.kicad_sch, triac-output.kicad_sch]
2020-11-19 some renderings
    [MadPresso.kicad_pcb]
2020-11-21 some more documentation
    [MadPresso.kicad_pcb, MadPresso.kicad_sch, ac-monitor.kicad_sch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]
2020-11-21 mechanical details for v1.1
    [MadPresso.kicad_pcb]
2020-12-02 started v1.2
    [BOM.ods, MadPresso.kicad_pcb, MadPresso.kicad_sch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]
2020-12-02 place debounce caps for mid400
    [MadPresso.kicad_sch, ac-monitor.kicad_sch]
2020-12-05 more clearance for LINE and NEUT
    [MadPresso.kicad_pcb]
2020-12-22 More updates
    * make pump triac switch NEUT, not LINE
    * move ADC a bit
    * improve clearance
    [MadPresso.kicad_pcb, MadPresso.kicad_sch, ac-monitor.kicad_sch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]
2020-12-22 Improve clearance
    [MadPresso.kicad_pcb, MadPresso.sch, triac-output.sch]
2020-12-22 change q7 to TO263 (D2PAK) package
    [MadPresso.kicad_pcb, MadPresso.kicad_sch, triac-output-to252.kicad_sch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]
2020-12-22 Revert Q7 back to DPAK
    [MadPresso.kicad_pcb, MadPresso.kicad_sch, ac-monitor.kicad_sch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]
2020-12-22 trace widths and clearance details
    [MadPresso.kicad_pcb]
2020-12-22 adc cleanups
    [MadPresso.kicad_pcb]
2020-12-22 update schematics pdf
2020-12-22 silkscreen fix
    [MadPresso.kicad_pcb]
2020-12-26 finializing v1.2
    [triac-output.kicad_sch]
2020-12-30 some more vias for neut triac
    [MadPresso.kicad_pcb]
2020-12-30 more cleanups, replace caps with ceramic types, polygon updates
    [BOM.ods, MadPresso.kicad_pcb, MadPresso.kicad_sch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]
2020-12-31 switch to ceramic caps
    [MadPresso.kicad_pcb, MadPresso.kicad_sch]
2021-01-01 re-add kicad logo
    [MadPresso.kicad_pcb]
2021-01-01 some minor details
    [MadPresso.kicad_pcb]
2021-01-02 remove stray track
    [MadPresso.kicad_pcb]
2021-01-08 Add v1.3
    * Fix footprints of MID400
    [BOM.ods, MadPresso.kicad_pcb, MadPresso.kicad_sch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]
2021-02-01 Change TRIAC type in schematics
    [MadPresso.kicad_pcb, MadPresso.kicad_sch, ac-monitor.kicad_sch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]
2021-03-27 add pictures of cables
